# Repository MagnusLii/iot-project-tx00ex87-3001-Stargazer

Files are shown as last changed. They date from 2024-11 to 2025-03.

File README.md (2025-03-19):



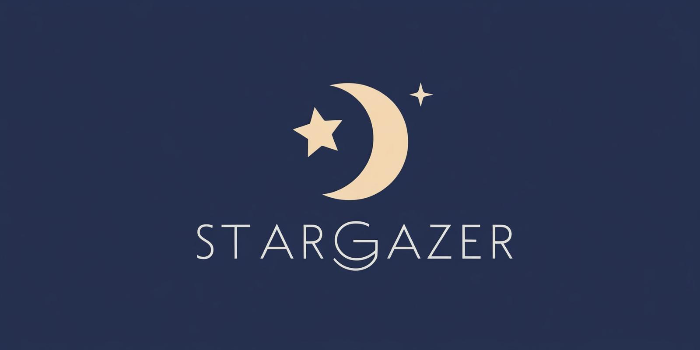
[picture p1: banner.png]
stargazer


  <p align="center">
    Amateur astronomy device

  </p>

<details>
  <summary>Table of Contents</summary>
  <ol>
    <li>
      <a href="#about-the-project">About The Project</a>
      <ul>
        <li><a href="#built-with">Built With</a></li>
      </ul>
    </li>
    <li>
      <a href="#getting-started">Getting Started</a>
      <ul>
        <li><a href="#prerequisites">Prerequisites</a></li>
        <li><a href="#installation">Installation</a></li>
      </ul>
    </li>
    <li><a href="#usage">Usage</a></li>
    <li><a href="#license">License</a></li>
  </ol>
</details>

## About The Project

The Stargazer is an easy to set up device that will take pictures of celestial objects at the most opportune times. Stargazer uses a simple and easy to use web interface to drive the device and see the beautiful pictures instantly when they happen. The pictures are also saved locally on an SD card for a convenient way of transferring and handling the pictures. Stargazer can also be driven completely offline using a laptop or a computer, making using the device flexible to use even when you have no internet connectivity.

### Built With

* [][Pico-SDK-url]
* [][ESP-idf-url]
* [][rustup-url]

## Getting Started

### Prerequisites

- ESP-idf: https://github.com/espressif/esp-idf
- Docker: https://www.docker.com/get-started/
- Rust: https://www.rust-lang.org/tools/install

See <a href="ASSEMBLY.md">ASSEMBLY.md</a> for details on building the physical device

**Optional:**
- Terminal connection software such as putty or minicom

### Installation

1. Clone the repo
   ```sh
   git clone https://gitlab.metropolia.fi/markulii/iot-project-tx00ex87-3001.git
   cd iot-project-tx00ex87-3001
   ```
2. Build Raspberry Pi Pico code with Docker
   ```sh
   cd pico
   docker compose up
   ```
3. Copy the binary to the Raspberry Pi Pico
    ```sh
    cp build/stargazer.uf2 <PATH TO PICO USB DEVICE PATH>
    ```

4. Build and flash ESP<br>
    Set the ESP into flash mode by connecting **GPIO0** to **GND** and power cycling the ESP.
    ```sh
    cd esp32-cam
    idf.py -p <PORT> flash
    ```
    Reboot the ESP out of flash mode by disconnecting **GPIO0** from **GND** and power cycling the ESP.
  
5. Build the webserver
   ```sh
   cd webserver
   ```
  - Option A. Build under repository directory
    ```sh
    cargo build --release
    ```
  - Option B. Build and install to Cargo install directory
    ```sh
    cargo install
    ```

## Usage

Run the server
  ```sh
    cargo run
  ```

* More details regarding the web server can be found <a href="webserver/README.md">here</a>

### Operating the device directly:
The device can be operated directly by connecting to the Pico via USB cable and opening a terminal connection with a baud rate of 115200.<br>
Sending any character puts the Pico into command mode which allows for using commands to operate the whole system.<br>

#### List of commands in configuration mode
`help` to see a list of all commands and their arguments.<br>
`exit` to exit command mode.<br>
`heading` to set compass heading of the device<br>
`time` to view or set current time<br>
`coord` to view or set current coordinates<br>
`instruction` to add an instruction directly to device<br>
`wifi` to set wifi details<br>
`server` to set the server details<br>
`token` to set the api token<br>

#### The following additional commands are available if debug build is compiled<br>

`debug_command` to add a command directly to the queue<br>
`debug_picture` to send a take picture message directly to the ESP<br>
`debug_rec_msg` to add a message (as if it came from the ESP) to the receive queue<br>
`debug_send_msg` to send a message to the ESP<br>
`debug_trace` to trace a planet with the device<br>

### Enabling operation from webserver:
When booting the device for the first time you'll need to provide the following for the Stargazer to connecto the webserver and run with full functionality.<br>
 - `Wifi SSID` - The ssid of your wireless network.
 - `Wifi password` - The password of your wireless network.
 - `Webserver domain` - The FQDN or IP address through which the server can be accessed.
 - `Webserver port` - The port used to communicated with the server (default is 8080).
 - `Webserver token` - Token generated in the webserver to enable API calls.

 **Optional:**

 - `Certificate` - Certificate to enable TLS connections. Only needed if you intend to use TLS to connect to your webserver.

 These settings can be set either by using the appropriate commands in direct control mode see: <a href="#direct-control">Operating the device directly:</a>

  alternatevly by setting them in a file called settings.txt on the SDcard connected to the ESP.<br>
  If creating the settings file the settings need to be in the same order as above with each setting on a new line.<br>
  The certificate needs to begin with `-----BEGIN CERTIFICATE-----` and end with `-----END CERTIFICATE-----`.

  **IMPORTANT:** The final line needs to include a 16bit crc in little endian ordering. A comma is prepended to the crc eg: `,4B37`<br>
  If any setting is missing or if the file is improperly formatted the device will not be able to initialize code/components related to said settings.<br>
  An example `settings.txt` can be found at <a href="example-settings.txt">/example-settings.txt.</a> <br>
  **NOTE:** the file must be renamed to `settings.txt`.<br>

  A third option is to define your values in `/esp32-cam/testMacros.hpp`, uncomment `# set(CMAKE_CXX_FLAGS "${CMAKE_CXX_FLAGS} -DSAVE_TEST_SETTINGS_TO_SDCARD")`<br>
  by removing the `#` in `/esp32-cam/CMakeLists.txt` and then build the project as described in <a href="#Build-and-flash-ESP">Build and flash ESP</a> <br>
  **NOTE:** Doing this will cause the settings defined in `/esp32-cam/testMacros.hpp` to be written onto `settings.txt` each time the ESP is restarted.

  <a href="#CMAKE-flags">Read here for more information about CMAKE flags</a> <br>

### Operating the device from the server:
The command options are as follows:<br>
* Target:<br>
`Sun`<br>`Moon`<br>`Mercury`<br>`Venus`<br>`Mars`<br>`Jupiter`<br>`Saturn`<br>`Uranus`<br>`Neptune`<br>
* Image Position:<br>
`Rising`: Takes a picture when the celestial object rises from the horizon.<br>
`Zenith`: Takes a picture at the zenith of the celestial object.<br>
`Setting`: Takes a picture when the celestial object close to setting beneath the horizon<br>
`Any`: Takes a picture at the current given time.<br>

## CMAKE flags
The following CMAKE flags can be enabled in <a href="esp32-cam/CMakeLists.txt">esp32-cam/CMakeLists.txt</a>.<br>
Enabling these flags changes the way the device operates.
 - set(CMAKE_CXX_FLAGS "${CMAKE_CXX_FLAGS} -DENABLE_ESP_DEBUG")<br>
   If enabled it will cause the ESP to send debug logs to the UART connection.<br>
   **NOTE:** These logs will cause problems for the pico and thus should not be turned on for normal operations, only if you wish to debug something.<br><br>
 - set(CMAKE_CXX_FLAGS "${CMAKE_CXX_FLAGS} -DUSE_TLS")<br>
   If enabled it will force the ESP to use TLS when connecting to the webserver.<br>
   **NOTE:** Due to the increased memory requirements of TLS this can cause the upload of larger images to fail due to insufficient memory on the AIthinker ESP32-cam module.<br><br>
 - set(CMAKE_CXX_FLAGS "${CMAKE_CXX_FLAGS} -DSAVE_TEST_SETTINGS_TO_SDCARD")<br>
   If enabled the ESP will write settings defined in `/esp32-cam/testMacros.hpp` to `settings.txt` on the SD card on boot.<br>
   This is useful if you do no wish to perform the other methods described in <a href="#Settings-file">Enabling operation from webserver</a>.<br>
   **NOTE:** Having this enabled will cause the settings to we written each time the ESP reboots causing settings to be lost if changed.

<!-- LICENSE -->
## License

Distributed under the ISC License. See `LICENSE` for more information.

<!-- MARKDOWN LINKS & IMAGES -->
<!-- https://www.markdownguide.org/basic-syntax/#reference-style-links -->
[contributors-shield]: https://img.shields.io/github/contributors/github_username/repo_name.svg?style=for-the-badge
[contributors-url]: https://github.com/github_username/repo_name/graphs/contributors

[repo-url]: https://gitlab.metropolia.fi/markulii/iot-project-tx00ex87-3001

[Pico-SDK-url]: https://github.com/raspberrypi/pico-sdk
[Pico-SDK-badge]: https://img.shields.io/badge/-RaspberryPi-C51A4A?style=for-the-badge&logo=Raspberry-Pi

[ESP-idf-url]: https://github.com/espressif/esp-idf
[ESP-IDF-badge]: https://img.shields.io/badge/Platform-ESP32-informational

[rustup-url]: https://www.rust-lang.org/tools/install
[rustup-badge]: https://img.shields.io/badge/Rust-%23000000.svg?e&logo=rust&logoColor=white&logoSize=20

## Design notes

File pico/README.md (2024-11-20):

# Building with Docker

1. Install Docker and Docker Compose
2. Run `docker compose up` in pico directory
3. After the build is complete, the binary will be available at `./build/pico-stargazer.{uf2|elf}` (Assuming it was successful)

# Flashing the Pico

## Using OpenOCD
- Make sure you have a Raspberry Pi Debug Probe or some other CMSIS-DAP device connected, and that you have OpenOCD installed (and in your PATH)
- Run the following command
```
$ openocd -f board/pico-debug.cfg -c "program build/pico-stargazer.elf verify reset exit"
```
- You may need to use `sudo` to run openocd depending on your system

## Copy the binary to the Pico
- Put the Pico into USB mass storage mode by holding down the BOOTSEL button and connecting it to your computer with a USB cable
- Copy the `pico-stargazer.uf2` file to the root of the USB drive

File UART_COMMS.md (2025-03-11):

## ESP & Pico communication
Protocol: UART<br>
Format: Custom Format<br>
example: `$<PREFIX>,<stuff>,<stuff2>,...<CRC>;`<br>
"$" Starts the message, ";" ends the message, `<PREFIX>` is the identifier for data, `<stuffX>` is data value.<br>

Celestial Object IDs:<br>
`<1>` = Sun<br>
`<2>` = Moon<br>
`<3>` = Mercury<br>
`<4>` = Venus<br>
`<5>` = Mars<br>
`<6>` = Jupiter<br>
`<7>` = Saturn<br>
`<8>` = Uranus<br>
`<9>` = Neptune<br>

Image position:<br>
`<1>` = Rising<br>
`<2>` = Zenith<br>
`<3>` = Setting<br>

Prefix values:<br>
`<0>` = unassigned/error<br>
`<1>` = ACK<br>
`<2>` = Datetime<br>
`<3>` = Device status check message<br>
`<4>` = ESP relaying command to Pico of what image to take.<br>
`<5>` = Command/Picture status from Pico to ESP<br>
`<6>` = Pico instructs ESP to take image<br>
`<7>` = Diagnostics data from Pico.         
`<8>` = WiFi information from Pico to ESP       
`<9>` = Send server ip/domain + (port) to ESP   
`<10>` = Api token from Pico to ESP             

Diagnostics values:<br>
`<1>` = Info<br>
`<2>` = Warning<br>
`<3>` = Error<br>

### Messages explained:

-   Datetime (Pico requests, ESP responds)<br>
    `$<2>,<1>,<CRC>;`<br>
    `$<2>,<Timestamp(int)>,<CRC>;` or `$<1>,<Bool>,<CRC>;` nack if not ready to send timestamp.<br>
    `$<1>,<Bool>,<CRC>;` True = ack, False nack.

-   Device init/status state message (ESP/Pico sends and other responds followed by final ack)<br>
    `$<3>,<Bool>,<CRC>;` True = ready, False = fire.<br>
    `$<3>,<Bool>,<CRC>;` True = ready, False = fire.<br>
    `$<1>,<Bool>,<CRC>;` True = ack, False nack.

-   Image taking process<br>
    ESP sends id of object to take picture of.<br>
    Pico sends (n)ack.<br>

    `$<4>,<Celestial object ID (int)>,<Image/command ID (int)>,<Position>,<CRC>;`<br>
    `$<1>,<Bool>,<CRC>;` True = ack, False nack.<br>

    Pico sends Command status message to ESP which it relays to the server.<br>
    ESP sends (n)ack.<br>

    `$<5>,<Image/command ID (int)>,<Status (int),<Time (int)>,<CRC>;`<br>
    `$<1>,<Bool>,<CRC>;` True = ack, False nack.<br>

    _Some time usually passes._<br>

    Pico sends take image message when the device is pointed at the celestial object and it's time to take a picture.<br>
    ESP takes picture and sends confirmation to Pico.<br>

    `$<6>,<Image/command ID (int)>,<CRC>;`<br>
    `$<1>,<Bool>,<CRC>;` True = ack, False nack.<br>

-   Diagnostics data from Pico.<br>
    `$<7>,<Status (int)>,<Message (string)>,<CRC>;`<br>
    `$<1>,<Bool>,<CRC>;` True = ack, False nack.<br>

-   Configuration messages from Pico.<br>

    Wi-Fi details<br>
    `$<8>,<SSID (string)>,<Password (string)>,<CRC>;`<br>
    `$<1>,<Bool>,<CRC>;` True = ack, False nack.<br>

    Server details<br>
    `$<9>,<IP/domain (string)>,<Port (int)>,<CRC>;` #if port = 0, port is unused<br>
    `$<1>,<Bool>,<CRC>;` True = ack, False nack.<br>

    API token<br>
    `$<10>,<Token (string)>,<CRC>;`<br>
    `$<1>,<Bool>,<CRC>;` True = ack, False nack.<br>

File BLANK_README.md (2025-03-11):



<h1 align="center">Stargazer</h1>

  <p align="center">
    Amateur astronomy device

  </p>

<details>
  <summary>Table of Contents</summary>
  <ol>
    <li>
      <a href="#about-the-project">About The Project</a>
      <ul>
        <li><a href="#built-with">Built With</a></li>
      </ul>
    </li>
    <li>
      <a href="#getting-started">Getting Started</a>
      <ul>
        <li><a href="#prerequisites">Prerequisites</a></li>
        <li><a href="#installation">Installation</a></li>
      </ul>
    </li>
    <li><a href="#usage">Usage</a></li>
    <li><a href="#license">License</a></li>
  </ol>
</details>

<!-- ABOUT THE PROJECT -->
## About The Project

The Stargazer is an easy to set up device that will take pictures of celestial objects at the most opportune times. Stargazer uses a simple and easy to use web interface to drive the device and see the beautiful pictures instantly when they happen. The pictures are also saved locally on an SD card for a convenient way of transferring and handling the pictures. Stargazer can also be driven completely offline using a laptop or a computer, making using the device flexible to use even when you have no internet connectivity.

<p align="right">(<a href="#readme-top">back to top</a>)</p>

### Built With

* [][Pico-SDK-url]
* [][ESP-idf-url]
* [][rustup-url]

<p align="right">(<a href="#readme-top">back to top</a>)</p>

## Getting Started

This is an example of how you may give instructions on setting up your project locally.
To get a local copy up and running follow these simple example steps.

### Prerequisites

This is an example of how to list things you need to use the software and how to install them.
- ESP-idf: https://github.com/espressif/esp-idf
- Docker: https://www.docker.com/get-started/
- Rust: https://www.rust-lang.org/tools/install

See <LINK TO ASSEMBLY MD> for details on building the physical device

optional:
- Terminal connection software such as putty or minicom

### Installation

1. Clone the repo
   ```sh
   git clone https://gitlab.metropolia.fi/markulii/iot-project-tx00ex87-3001.git
   cd iot-project-tx00ex87-3001
   ```
2. Build Raspberry Pi Pico code with Docker
   ```sh
   cd pico
   docker compose up
   ```
3. Copy the binary to the Raspberry Pi Pico
    ```sh
    cp build/stargazer.uf2 <PATH TO PICO USB DEVICE PATH>
    ```
4. Build and flash ESP<br>
    Set the ESP into flash mode.
    ```sh
    cd esp32-cam
    idf.py -p <PORT> flash
    ```
    Reboot the ESP out of flash mode.
  
5. Build the webserver
   ```sh
   cd webserver
   ```
  - Option A. Build under repository directory
    ```sh
    cargo build --release
    ```
  - Option B. Build and install to Cargo install directory
    ```sh
    cargo install
    ```

<p align="right">(<a href="#readme-top">back to top</a>)</p>

## Usage

Run the server
  ```sh
    cargo run
  ```

### - Operating the device directly:
The device can be operated directly by connecting to the Pico via USB cable and opening a terminal connection with a baud rate of 115200.<br>
Sending any character puts the Pico into command mode which allows for using commands to operate the whole system.<br>

#### List of commands in configuration mode
`help` to see a list of all commands and their arguments.<br>
`exit` to exit command mode.<br>
`heading` to set compass heading of the device<br>
`time` to view or set current time<br>
`coord` to view or set current coordinates<br>
`instruction` to add an instruction directly to device<br>
`wifi` to set wifi details<br>
`server` to set the server details<br>
`token` to set the api token<br>

#### The following additional commands are available if debug build is compiled<br>

`debug_command` to add a command directly to the queue<br>
`debug_picture` to send a take picture message directly to the ESP<br>
`debug_rec_msg` to add a message (as if it came from the ESP) to the receive queue<br>
`debug_send_msg` to send a message to the ESP<br>
`debug_trace` to trace a planet with the device<br>

### Enabling operation from webserver:
When booting the device for the first time you'll need to provide the following for the Stargazer to connecto the webserver and run with full functionality.<br>
 - `Wifi SSID` - The ssid of your wireless network.
 - `Wifi password` - The password of your wireless network.
 - `Webserver domain` - The FQDN or IP address through which the server can be accessed.
 - `Webserver port` - The port used to communicated with the server (default is 8080).
 - `Webserver token` - Token generated in the webserver to enable API calls.
 Optional:
 - `Certificate` - Certificate to enable TLS connections. Only needed if you intend to use TLS to connect to your webserver.

 These settings can be set either by using the appropriate commands in direct control mode see: 
 
 <p align="left"><a href="#direct-control">### - Operating the device directly:</a></p>

  or by setting them in a file called settings.txt on the SDcard connected to the ESP.<br>
  If creating the settings file the settings need to be in the same order as above with each setting on a new line.<br>
  The certificate needs to begin with `-----BEGIN CERTIFICATE-----` and end with `-----END CERTIFICATE-----`.

  IMPORTANT: The final line needs to include a 16bit crc in little endian ordering. A comma is prepended to the crc eg: `,4B37`<br>
  If any setting is missing or if the file is improperly formatted the device will not be able to initialize code/components related to   said settings.

### Operating the device from the server:
The command options are as follows:<br>
* Target:<br>
`Sun`<br>`Moon`<br>`Mercury`<br>`Venus`<br>`Mars`<br>`Jupiter`<br>`Saturn`<br>`Uranus`<br>`Neptune`<br>
* Image Position:<br>
`Rising`: Takes a picture when the celestial object rises from the horizon.<br>
`Zenith`: Takes a picture at the zenith of the celestial object.<br>
`Any`: Takes a picture at the current given time.<br>

<p align="right">(<a href="#readme-top">back to top</a>)</p>

<!-- LICENSE -->
## License

Distributed under the ISC License. See `LICENSE` for more information.

<p align="right">(<a href="#readme-top">back to top</a>)</p>

<!-- MARKDOWN LINKS & IMAGES -->
<!-- https://www.markdownguide.org/basic-syntax/#reference-style-links -->
[contributors-shield]: https://img.shields.io/github/contributors/github_username/repo_name.svg?style=for-the-badge
[contributors-url]: https://github.com/github_username/repo_name/graphs/contributors

[repo-url]: https://gitlab.metropolia.fi/markulii/iot-project-tx00ex87-3001

[Pico-SDK-url]: https://github.com/raspberrypi/pico-sdk
[Pico-SDK-badge]: https://img.shields.io/badge/-RaspberryPi-C51A4A?style=for-the-badge&logo=Raspberry-Pi

[ESP-idf-url]: https://github.com/espressif/esp-idf
[ESP-IDF-badge]: https://img.shields.io/badge/Platform-ESP32-informational

[rustup-url]: https://www.rust-lang.org/tools/install
[rustup-badge]: https://img.shields.io/badge/Rust-%23000000.svg?e&logo=rust&logoColor=white&logoSize=20

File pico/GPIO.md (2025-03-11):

#  PINS
### 1 - GP0       - UART0 TX - ESP RX
### 2 - GP1       - UART0 RX - ESP TX
### 3 - GND       - 
### 4 - GP2       - 
### 5 - GP3       - 
### 6 - GP4       - UART1 TX - GPS RX
### 7 - GP5       - UART1 RX - GPS TX
### 8 - GND       - 
### 9 - GP6       - LN4 - MOTOR HORIZONTAL
### 10 - GP7      - LN3 - MOTOR HORIZONTAL
### 11 - GP8      - LN2 - MOTOR HORIZONTAL
### 12 - GP9      - LN1 - MOTOR HORIZONTAL
### 13 - GND      - 
### 14 - GP10     - OPTO HORIZONTAL
### 15 - GP11     - 
### 16 - GP12     - 
### 17 - GP13     - 
### 18 - GND      - 
### 19 - GP14     - 
### 20 - GP15     - OPTO VERTICAL
### 21 - GP16     - I2C0 SDA - COMPASS
### 22 - GP17     - I2C0 SCL - COMPASS
### 23 - GND      - 
### 24 - GP18     - LN4 - MOTOR VERTICAL
### 25 - GP19     - LN3 - MOTOR VERTICAL
### 26 - GP20     - LN2 - MOTOR VERTICAL
### 27 - GP21     - LN1 - MOTOR VERTICAL
### 28 - GND      - 
### 29 - GP22     - 
### 30 - RUN      - 
### 31 - GP26     - I2C1 SDA - EEPROM
### 32 - GP27     - I2C1 SCL - EEPROM
### 33 - GND      - 
### 34 - GP28     - 
### 35 - ADC_VREF -  
### 36 - 3V3OUT   - 
### 37 - 3V3EN    - 
### 38 - GND      - GND - ESP (any ground pin will do)
### 39 - VSYS     - 5V - ESP
### 40 - VBUS     -

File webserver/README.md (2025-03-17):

# Requirements
- Cargo/rustc (build, tested on version 1.84)

# Building

## Option A. Build only
```sh
cargo build --release
```
## Option B. Build and install to Cargo binary directory
```sh
cargo install
```

# Configuration
Server configuration can be set in a `config.toml` file which the program will look for in the current working directory by default.<br>

You can also specify a config file as an argument to the program.<br>

All available configuration options can be found in the <a href="example-config.toml">example-config.toml</a>

# Usage
```
Stargazer webserver

Usage: stargazer-ws [OPTIONS]

Options:
  -a, --address <ADDRESS>          Set server address
  -p, --port-http <PORT_HTTP>      Set HTTP port
  -s, --port-https <PORT_HTTPS>    Set HTTPS port
      --disable-http               Disable HTTP
      --enable-http                Enable HTTP
      --enable-http-api            Enable HTTP API if HTTP is disabled
      --disable-https              Disable HTTPS
      --enable-https               Enable HTTPS
      --enable-https-api           Enable HTTPS API if HTTPS is disabled
  -c, --config-file <CONFIG_FILE>  Set config file to use (default: config.toml)
  -w, --working-dir <WORKING_DIR>  Set working directory
      --db-dir <DB_DIR>            Set database directory
      --assets-dir <ASSETS_DIR>    Set assets directory
      --certs-dir <CERTS_DIR>      Set certificate directory
  -h, --help                       Print help
  -V, --version                    Print version
```

## Option A
#### You can run the server using
```sh
cargo run --
```
#### or by running the executable directly (located under target/<build_type>/)
```sh
cd target/release/
./stargazer-ws
```

## Option B
#### You can run the server from anywhere (provided that the Cargo bin dir is in your path)
```sh
stargazer-ws
```

## Web interface
When starting up the server for the first time you can login using the default credentials:<br>
Username: admin<br>
Password: admin<br>

* You can change the username and/or password of the admin account on the user page, which you can get to by clicking the account name in the navigation bar/menu.<br>

### Quick start instructions

You need to first create a key from the `Keys` page which can be accessed from the `Control` page before you can add commands to the queue.<br>
Generating a key is as simple as giving it a name then pressing generate.<br>
Then you can copy and give the key/token to the Stargazer device<br><br>

After that is done you can add commands from the `Control`/`Commands` page.<br>

The command options are as follows:<br>
* Target:<br>
`Sun`<br>`Moon`<br>`Mercury`<br>`Venus`<br>`Mars`<br>`Jupiter`<br>`Saturn`<br>`Uranus`<br>`Neptune`<br>
* Image Position:<br>
`Rising`: Takes a picture when the celestial object rises from the horizon.<br>
`Zenith`: Takes a picture at the zenith of the celestial object.<br>
`Setting`: Takes a picture when the celestial object close to setting beneath the horizon
`Any`: Takes a picture at the current given time.<br>

# API
The API currently has the following endpoints:

- `/api/upload` (POST)
- `/api/command` (GET, POST)
- `/api/diagnostics` (POST)
- `/api/time` (GET)

More details can be found in API.md

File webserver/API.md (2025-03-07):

# API
The API currently has the following endpoints:

- `/api/upload` (POST)
- `/api/command` (GET, POST)
- `/api/diagnostics` (POST)
- `/api/time` (GET)

## `/api/upload`
Uploads an image wrapped in JSON to the webserver.

The JSON should contain the following fields:

- `token`: The API token (string)
- `id`: The ID of the command (int)
- `data`: The base64 encoded image (string)

Example:
```
curl -H "Content-Type: application/json" --request POST --data @img.json 127.0.0.1:7878/api/upload
```
where @img.json contains:
```
{
    "token":"<api_token>",
    "id":<id>,
    "data":"<base64_data>"
}
```

## `/api/command`
### GET
Fetch a command from the webserver.

Example:
```
curl "127.0.0.1:7878/api/command?token=<api_token>"
```

Returns a JSON object with the following fields:
- `target`: The target object (int)
- `id`: The ID of the command/picture (int)
- `position`: The position to take the photo (int) {1,2,3}

Or an empty object if no command is available

### POST
Send a response in JSON to the webserver.

The JSON should contain the following fields:

- `token`: The API token (string)
- `id`: The ID of the command (int)
- `status`: The command status (int)
```
Command status: (-)1 = Fetch, (-)2 = Calculate, ((-)3 = Picture)
Negative sign indicates error in said stage.
```

Optional fields:
- `time`: The estimated time to take the photo (int) [NOTE: unix epoch time sent along with status 2]

Example:
```
curl -H "Content-Type: application/json" --request POST --data "{\"token\":\"ae07ddd0-5dc1-47d2-98ab-9cea274f1f61\",\"id\":1,\"status\":2}" 127.0.0.1:7878/api/command
```

## `/api/diagnostics`
Send diagnostics to the webserver.

The JSON should contain the following fields:

- `token`: The API token (string)
- `status`: The status (int)
- `message`: The message (string)

## `/api/time`
Get the current time from the webserver.

Example:
```
curl "127.0.0.1:7878/api/time"
```

Returns time in seconds since epoch

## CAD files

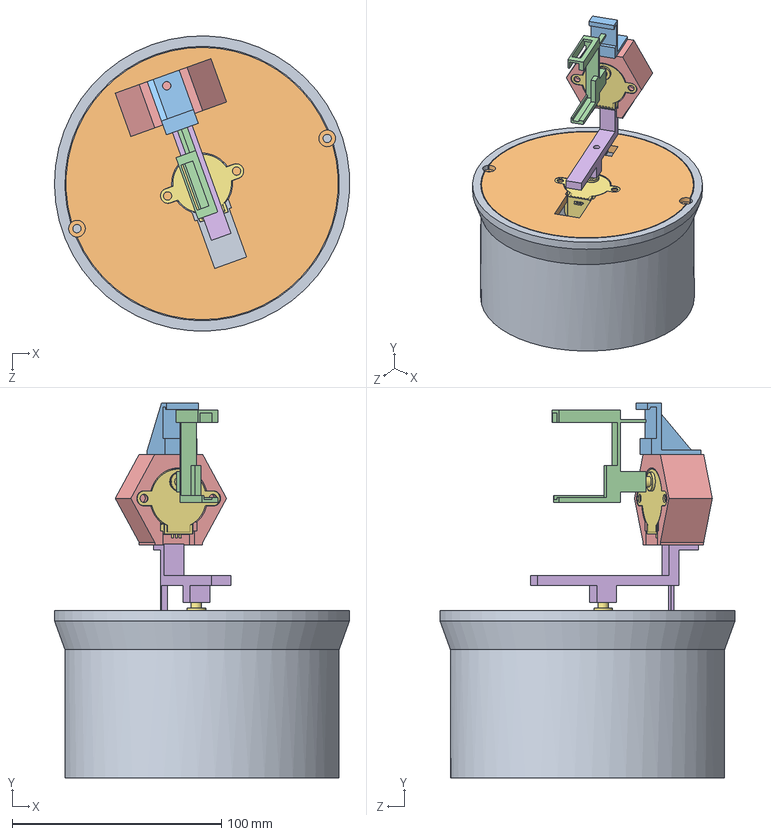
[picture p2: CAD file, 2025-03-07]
3D-models/Gyro-arm-assembly.SLDASM
140.9 x 179.0 x 140.9 mm
28BYJ-48-stepper-motor x 2
Connector-arm
28BYJ-48-cover
ESP-Holder
Opto-fork-holder
28BYJ-48-bottom-plate
Bottom-bowl

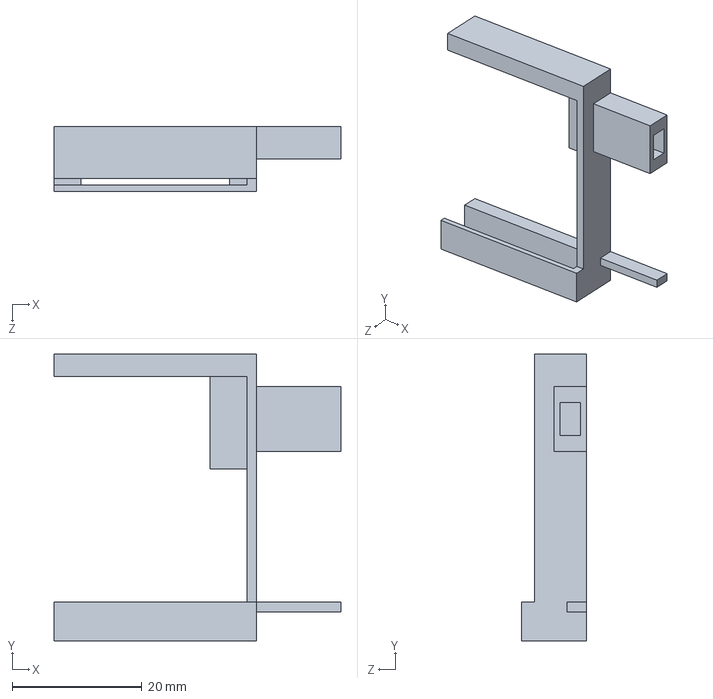
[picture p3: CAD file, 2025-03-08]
3D-models/ESP-Holder.SLDPRT
44.2 x 44.2 x 10.0 mm

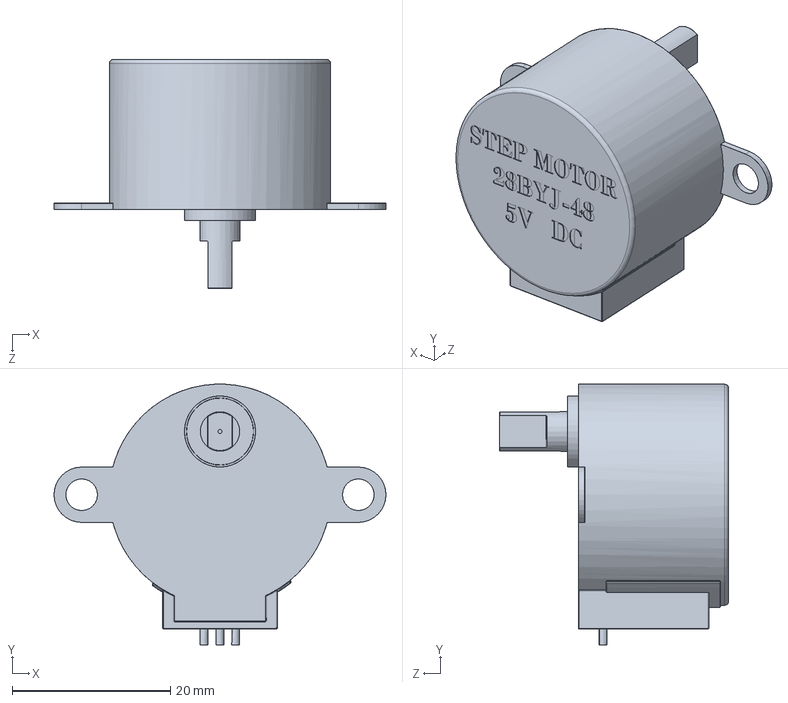
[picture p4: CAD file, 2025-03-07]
3D-models/28BYJ-48-stepper-motor.sldprt
42.0 x 33.0 x 29.0 mm

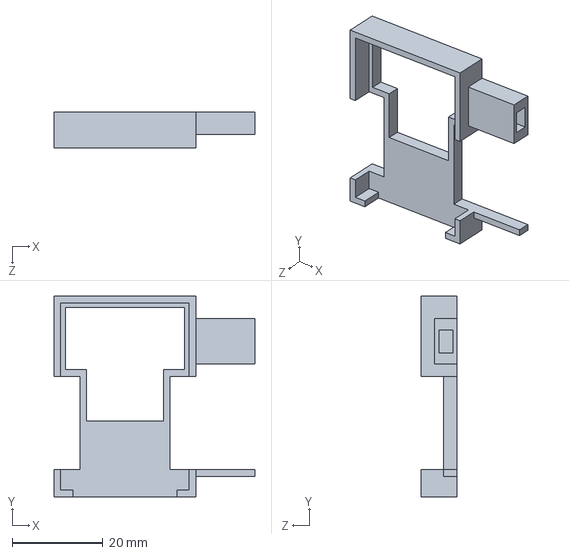
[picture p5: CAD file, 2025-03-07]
3D-models/ESP-Holder - BACKUP.SLDPRT
44.2 x 44.2 x 8.00 mm

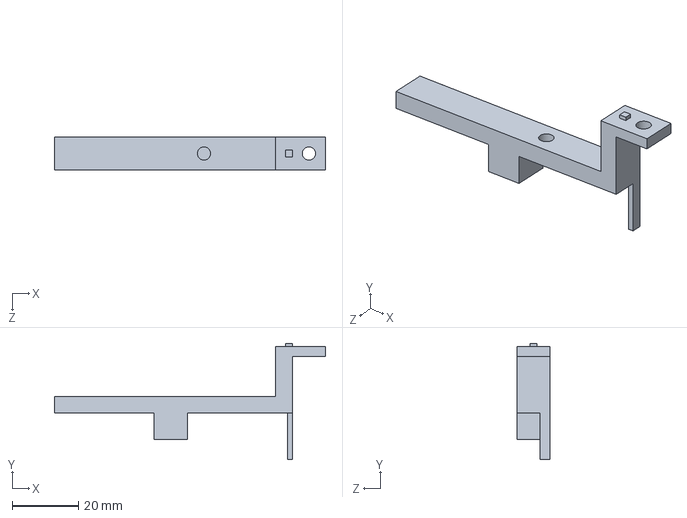
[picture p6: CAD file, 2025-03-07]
3D-models/Connector-arm.SLDPRT
81.6 x 35.0 x 10.0 mm

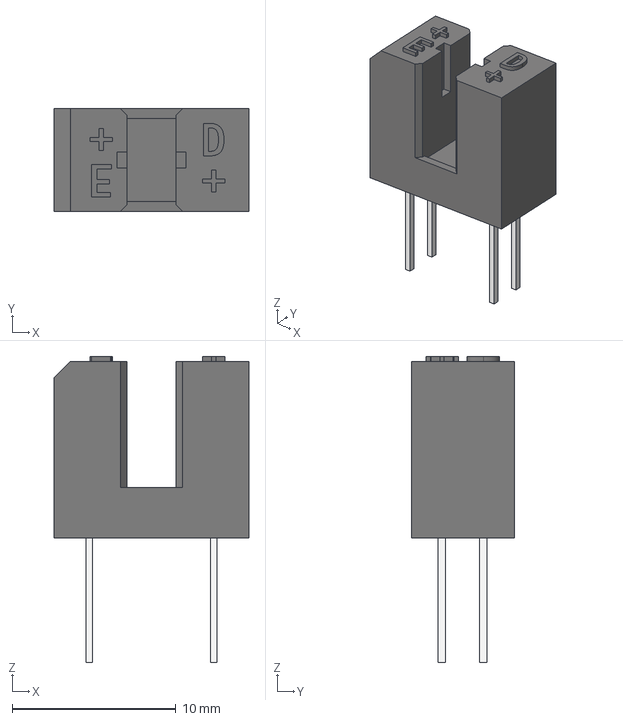
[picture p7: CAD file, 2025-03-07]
3D-models/TCST1103.stp
11.9 x 6.30 x 18.7 mm

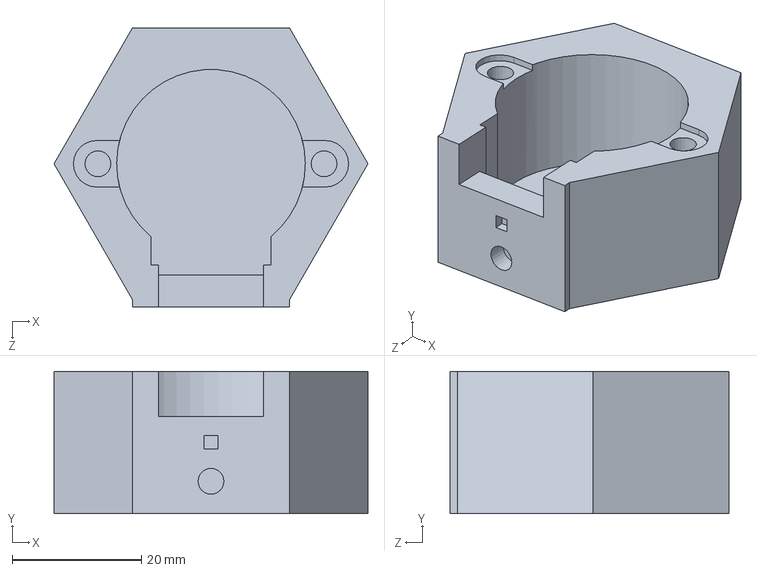
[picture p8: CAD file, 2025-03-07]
3D-models/28BYJ-48-cover.SLDPRT
48.6 x 22.0 x 43.2 mm

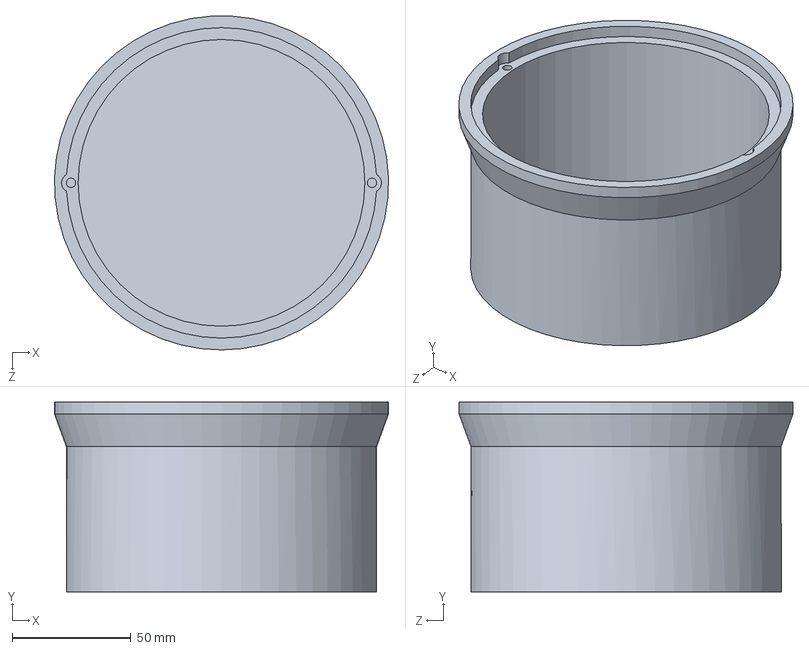
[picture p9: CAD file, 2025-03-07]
3D-models/Bottom-bowl.SLDPRT
140.9 x 80.0 x 140.9 mm

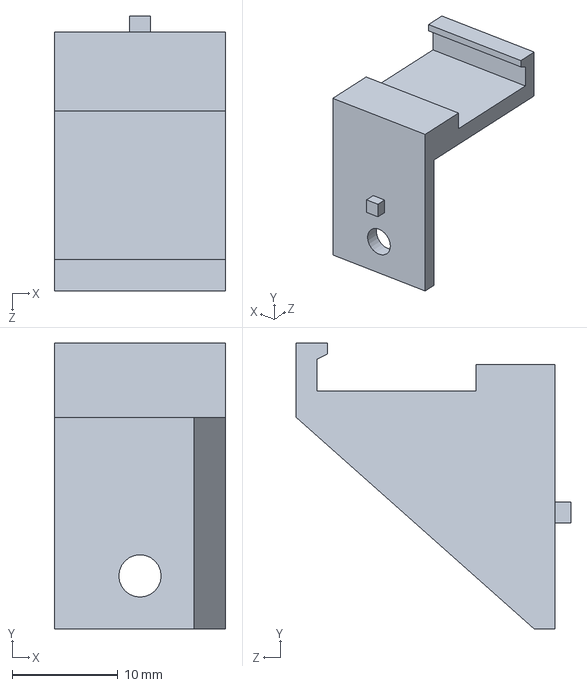
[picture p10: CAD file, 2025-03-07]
3D-models/Opto-fork-holder.SLDPRT
16.2 x 27.0 x 26.0 mm

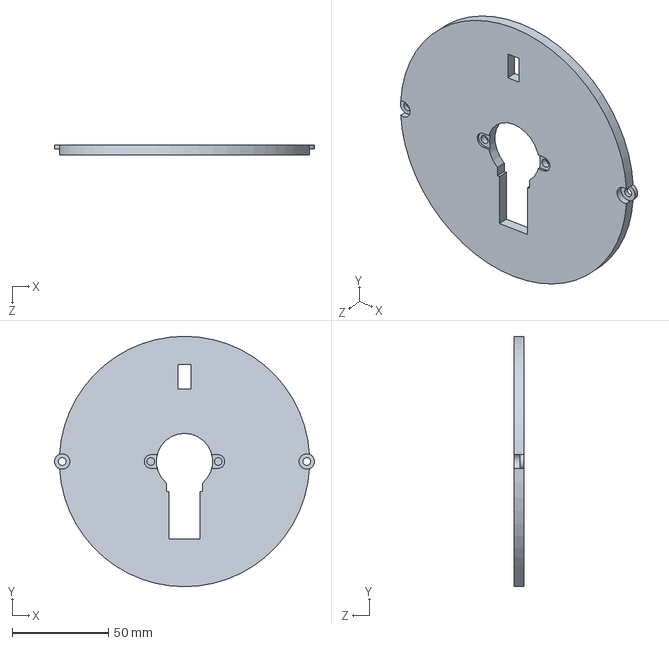
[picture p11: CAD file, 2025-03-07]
3D-models/28BYJ-48-bottom-plate.SLDPRT
135.0 x 130.0 x 5.00 mm

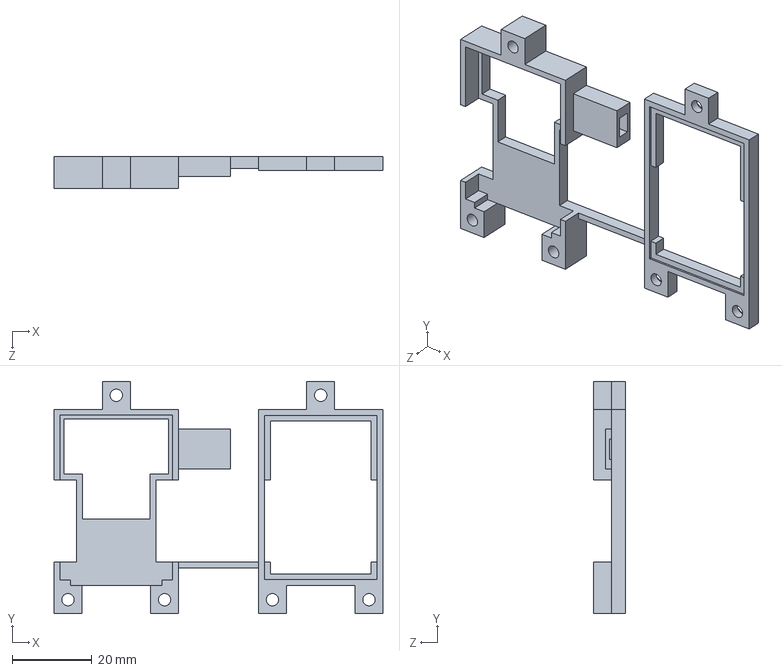
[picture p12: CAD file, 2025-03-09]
3D-models/ESP-Holder-Nut-Lock-Design.SLDPRT
82.4 x 58.2 x 8.00 mm

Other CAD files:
3D-models/STL/28BYJ-48-bottom-plate.STL
3D-models/STL/28BYJ-48-cover.STL
3D-models/STL/Bottom-bowl.STL
3D-models/STL/Connector-arm.STL
3D-models/STL/ESP-Holder-Nut-Lock-Design.STL
3D-models/STL/ESP-Holder.STL
3D-models/STL/Opto-fork-holder.STL

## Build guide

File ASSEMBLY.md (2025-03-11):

# Instructions for assembling the Stargazer

## Requirements
- 3D printer
- 8 M3-0.5 heat inserts
- 8 M3 screws
- Electrical tape
- Pico or PicoW (H or WH versions also work)
- AIthinker esp-cam32
- Jumper wires
- 2 grove cables
- 2 28BYJ-48 stepper motors
- 2 6pin Stepper motor drivers
- Crowtail three-axis compass
- Mikroe GPS3 click gps
- Crowtail I2C EEPROM
- 2 TCST1103 opto forks

optional:
- Soldering board(s)

if using nut-lock version of ESP-Holder:<br>
- 3 M3 screws
- 3 M3 nuts

## 3D prints
STL files for printing can be found under `/3D-models/STL`.<br>
Files for 3D models can be found under `/3D-models`.<br>

3D-Models/Gyro-arm-assembly.SLDASM can be used to view the entire assembly as intended to be assembled in solidworks.<br>

Note: There are two files for ESP-holder, both designs work however one locks the ESP more securely. Only one is needed for the Stargazer.

## Assembly

### 3D printed parts and components
Some of the parts are designed to have M3-0.5 heat inserts inserted into them to enable using screws to securely connect the parts.<br>
- The <a href="3D-models/STL/Bottom-bowl.STL">Bottom-bowl</a> is mean to contain most of the electronics and and acts as the stand for the Stargazer.<br>
- The <a href="3D-models/STL/28BYJ-48-bottom-plate.STL">28BYJ-48-Bottom-plate</a> acts as a cover for the bowl and a platform for the camera gyro setup.<br>
Two screw placements are provided to securely mount the plate to the bowl. The plate has a hole for the horizontal bottom motor and opto fork sensor.<br>
There are two insert holes next to the central motor hole to screw the motor onto the plate.<br>
- The <a href="3D-models/STL/Connector-arm.STL">Connector-arm</a> connects the bottom horizontal motor to the <a href="3D-models/STL/28BYJ-48-cover.STL">28BYJ-48-cover</a> which houses the top vertical motor. This connection requres one screw/insert.
- The <a href="3D-models/STL/Opto-fork-holder.STL">Opto-fork-holder</a> is placed ontop of the <a href="3D-models/STL/Connector-arm.STL">Connector-arm</a> and is meant to hold the vertical TCST1103 opto fork. Note our opto forks has custom printed circuit boards which we do not have the files for there fore this <a href="3D-models/STL/Opto-fork-holder.STL">Opto-fork-holder</a> design will not work with most cases.
- And finally the <a href="3D-models/STL/ESP-Holder-Nut-Lock-Design.STL">ESP-Holder</a> connects to the vertical motor without screws and holds the ESP.
- All the other components are located in the bottom bowl.

### Microcontroller wiring
Wiring pins can be seen in <a href="pico/GPIO.md">pico/GPIO.MD</a>, all other devices/motors/sensors are wired directly to the Pico.

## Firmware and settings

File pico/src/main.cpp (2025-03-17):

#include "pico/stdlib.h" // IWYU pragma: keep

#include "PicoUart.hpp"
#include "clock.hpp"
#include "commbridge.hpp"
#include "compass.hpp"
#include "controller.hpp"
#include "debug.hpp"
#include "gps.hpp"
#include "message.hpp"
#include "motor-control.hpp"
#include "stepper-motor.hpp"
#include "storage.hpp"

#include <memory>
#include <queue>

int main() {
    stdio_init_all();
    sleep_ms(500);
    DEBUG("Boot");

    auto uart_0 = std::make_shared<PicoUart>(0, 0, 1, 115200);
    DEBUG("UART0 initialized");
    auto uart_1 = std::make_shared<PicoUart>(1, 4, 5, 9600);
    DEBUG("UART1 initialized");
    sleep_ms(50);

    auto clock = std::make_shared<Clock>();
    DEBUG("Clock initialized");
    auto gps = std::make_shared<GPS>(uart_1, false, true);
    DEBUG("GPS initialized");
    auto compass = std::make_shared<Compass>(i2c0, 17, 16);
    DEBUG("Compass initialized");
    auto storage = std::make_shared<Storage>(i2c1, 26, 27);

    auto queue = std::make_shared<std::queue<msg::Message>>();
    DEBUG("Queue initialized");
    auto commbridge = std::make_shared<CommBridge>(uart_0, queue);
    DEBUG("CommBridge initialized");

    const std::vector<uint> pins1{6, 7, 8, 9};
    DEBUG("Stepper motor pins initialized");
    const std::vector<uint> pins2{18, 19, 20, 21};
    DEBUG("Stepper motor pins initialized");
    const int opto_horizontal = 10;
    const int opto_vertical = 15;

    auto mh = std::make_shared<StepperMotor>(pins1);
    DEBUG("Stepper motor initialized");
    auto mv = std::make_shared<StepperMotor>(pins2);
    DEBUG("Stepper motor initialized");
    auto mctrl = std::make_shared<MotorControl>(mh, mv, opto_horizontal, opto_vertical);
    DEBUG("MotorControl initialized");

    Controller controller(clock, gps, compass, commbridge, mctrl, storage, queue);
    DEBUG("Controller initialized");
    for (;;) {
        controller.run();

        DEBUG("Returned from main loop");
        sleep_ms(1000);
    }
}

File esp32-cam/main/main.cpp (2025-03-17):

#include <esp_event.h>
#include <esp_log.h>
#include <esp_system.h>
#include <nvs_flash.h>
#include <stdio.h>
#include <stdlib.h>
#include <sys/param.h>

#include "freertos/FreeRTOS.h"
#include "freertos/task.h"

#include "driver/sdmmc_defs.h"
#include "driver/sdmmc_host.h"
#include "esp_vfs_fat.h"
#include "sdmmc_cmd.h"

#include "TaskPriorities.hpp"
#include "camera.hpp"
#include "debug.hpp"
#include "requestHandler.hpp"
#include "sd-card.hpp"
#include "testMacros.hpp"
#include "wireless.hpp"
#include <memory>

#include "esp_sntp.h"
#include "tasks.hpp"
#include "timesync-lib.hpp"

#include "espPicoUartCommHandler.hpp"
#include "message.hpp"

#include "esp_task_wdt.h"

#include "mbedtls/platform.h"

#include <set>

extern "C" {
void app_main(void);
}
void app_main(void) {
    DEBUG("Starting main");
    vTaskDelay(pdMS_TO_TICKS(1000));

    xTaskCreate(init_task, "init-task", 8192, NULL, TaskPriorities::HIGH, NULL);

    while (1) {
        vTaskDelay(pdMS_TO_TICKS(10000));
    }
}

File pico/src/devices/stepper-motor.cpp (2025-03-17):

#include "stepper-motor.hpp"
#include "stepper.pio.h"
#include "structs.hpp"

int modulo(int x, int y) {
    int rem = x % y;
    return rem + ((rem < 0) ? y : 0);
}

StepperMotor::StepperMotor(const std::vector<uint> &stepper_pins)
    : pins(stepper_pins), direction(true), pioInstance(nullptr), programOffset(0), stateMachine(0), speed(0),
      sequenceCounter(0), stepCounter(0), stepMax(4097), stepMemory(0) {
    // need 4 pins
    if (pins.size() != 4) panic("Need 4 pins to operate stepper motor. number of pins got: %d", pins.size());
    // Three first stepper pins must be less than 6 apart
    if (pins[2] - pins[0] > 5)
        panic("Three first stepper pins must be less than 6 apart. They are %d apart", pins[2] - pins[0]);
}

void StepperMotor::init(PIO pio, float rpm, bool clockwise) {
    pioInstance = pio;
    speed = rpm;
    direction = clockwise;
    pioInit();
    pins_init();
    pio_sm_set_enabled(pioInstance, stateMachine, true);
}

// this doesn't set the statemachine running
void StepperMotor::pioInit(void) {
    if (direction) {
        programOffset = pio_add_program(pioInstance, &stepper_clockwise_program);
    } else {
        programOffset = pio_add_program(pioInstance, &stepper_anticlockwise_program);
    }
    pio_sm_config conf = stepper_clockwise_program_get_default_config(programOffset);
    sm_config_set_clkdiv(&conf, calculateClkDiv(speed));
    stateMachine = pio_claim_unused_sm(pioInstance, true);
    pio_sm_init(pioInstance, stateMachine, programOffset, &conf);
}

float StepperMotor::calculateClkDiv(float rpm) const {
    if (rpm > RPM_MAX) rpm = RPM_MAX;
    if (rpm < RPM_MIN) rpm = RPM_MIN;
    return (SYS_CLK_KHZ * 1000) / (16000 / (((1 / rpm) * 60 * 1000) / 4096));
}

// needs to be called after initializing PIO and statemachine
// The pins have to be ascending in order
void StepperMotor::pins_init() {
    // mask is needed to set pin directions in the state machine
    uint32_t pin_mask = 0x0;
    for (uint pin : pins) {
        pin_mask |= 1 << pin;
        pio_gpio_init(pioInstance, pin);
    }
    pio_sm_set_pindirs_with_mask(pioInstance, stateMachine, pin_mask, pin_mask);
    // Configure the set pins (first 3 pins) and the sideset pin (last pin)
    pio_sm_set_set_pins(pioInstance, stateMachine, pins[0], pins[2] - pins[0] + 1);
    pio_sm_set_sideset_pins(pioInstance, stateMachine, pins[3]);
    // this changes the statemachines bytecode to match the pins used.
    morph_pio_pin_definitions();
}

// this needs to be ran everytime the program changes!! (changing directions etc)
// changes the statemachines bytecode to match the pin layout
void StepperMotor::morph_pio_pin_definitions(void) {
    // TODO: make a cool equation to reduce code duplication
    uint pin1 = 1;
    uint pin2 = 1 << (pins[1] - pins[0]);
    uint pin3 = 1 << (pins[2] - pins[0]);
    std::vector<uint> instructions;
    instructions.reserve(8);
    // pin1
    instructions.emplace_back(pio_encode_set(pio_pins, pin1) | pio_encode_delay(7) | pio_encode_sideset(2, 0b10));
    // pin1 and 2
    instructions.emplace_back(pio_encode_set(pio_pins, pin1 | pin2) | pio_encode_delay(7) |
                              pio_encode_sideset(2, 0b10));
    // pin2
    instructions.emplace_back(pio_encode_set(pio_pins, pin2) | pio_encode_delay(7) | pio_encode_sideset(2, 0b10));
    // pin2 and pin 3
    instructions.emplace_back(pio_encode_set(pio_pins, pin2 | pin3) | pio_encode_delay(7) |
                              pio_encode_sideset(2, 0b10));
    // pin3
    instructions.emplace_back(pio_encode_set(pio_pins, pin3) | pio_encode_delay(7) | pio_encode_sideset(2, 0b10));
    // pin3 and pin4 (sideset)
    instructions.emplace_back(pio_encode_set(pio_pins, pin3) | pio_encode_delay(7) | pio_encode_sideset(2, 0b11));
    // no first 3 pins active pin4 active (sideset)
    instructions.emplace_back(pio_encode_set(pio_pins, 0) | pio_encode_delay(7) | pio_encode_sideset(2, 0b11));
    // pin1 and pin4 (sideset)
    instructions.emplace_back(pio_encode_set(pio_pins, pin1) | pio_encode_delay(7) | pio_encode_sideset(2, 0b11));
    if (!direction) { std::reverse(instructions.begin(), instructions.end()); }
    for (int i = 0; i < 8; i++) {
        pioInstance->instr_mem[programOffset + stepper_clockwise_offset_loop + i * 3] = instructions[i];
    }
}

void StepperMotor::turnSteps(uint16_t steps) {
    uint32_t word = ((programOffset + stepper_clockwise_offset_loop + 3 * sequenceCounter) << 16) | (steps);
    pio_sm_put_blocking(pioInstance, stateMachine, word);

    sequenceCounter = modulo(sequenceCounter + steps, 8);
    int16_t stepsToAdd = direction ? steps : -steps;
    stepCounter = modulo(stepCounter + stepsToAdd, stepMax);
    stepMemory = (stepMemory << 16) | stepsToAdd;
}

// this will stop the motor and turn to an angle instantly
void StepperMotor::turn_to(double radians) {
    stop();
    double current = get_position();
    double normalized = normalize_radians(radians);
    double distance = normalized - current;
    if (distance < -M_PI) { distance += 2 * M_PI; }
    if (distance > M_PI) { distance -= 2 * M_PI; }
    if (distance < 0)
        setDirection(ANTICLOCKWISE);
    else
        setDirection(CLOCKWISE);
    turnSteps(radians_to_steps(fabs(distance)));
}

void StepperMotor::turnOneRevolution() { turnSteps(stepMax); }

void StepperMotor::setSpeed(float rpm) {
    pio_sm_set_enabled(pioInstance, stateMachine, false);
    speed = rpm;
    float div = calculateClkDiv(rpm);
    pio_sm_set_clkdiv(pioInstance, stateMachine, div);
    pio_sm_set_enabled(pioInstance, stateMachine, true);
}

void StepperMotor::resetStepCounter(void) { stepCounter = 0; }

void StepperMotor::stop() {
    pio_sm_set_enabled(pioInstance, stateMachine, false);

    sequenceCounter = modulo(getCurrentStep() + 1, 8);
    if (direction == ANTICLOCKWISE) { sequenceCounter = modulo(7 - (sequenceCounter - 1) + 1, 8); }
    uint fifoLevel = pio_sm_get_tx_fifo_level(pioInstance, stateMachine);
    int32_t stepsLeft = read_steps_left();
    stepCounter = modulo(stepCounter - stepsLeft, stepMax);

    for (uint i = 0; i < fifoLevel; i++) {
        stepCounter = modulo(stepCounter - (int16_t)(stepMemory & 0xffff), stepMax);
        stepMemory >>= 16;
    }

    pio_sm_clear_fifos(pioInstance, stateMachine);
    pio_sm_exec(pioInstance, stateMachine, pio_encode_jmp(0));
    pio_sm_set_enabled(pioInstance, stateMachine, true);
}

void StepperMotor::off() {
    // TODO: make this work
    uint instr = pio_encode_set(pio_pins, 0) | pio_encode_sideset(2, 0);
    pio_sm_exec(pioInstance, stateMachine, instr);
    return;
}
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

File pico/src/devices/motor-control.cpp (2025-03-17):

#include "motor-control.hpp"

#define NATURAL_SPEED 3

// these are used for calibration
static MotorControl *motorcontrol;

MotorControl::MotorControl(std::shared_ptr<StepperMotor> horizontal, std::shared_ptr<StepperMotor> vertical,
                           int optopin_horizontal, int optopin_vertical)
    : motor_horizontal(horizontal), motor_vertical(vertical), opto_horizontal(optopin_horizontal),
      opto_vertical(optopin_vertical), horizontal_calibrated(false), vertical_calibrated(false),
      horizontal_calibrating(false), vertical_calibrating(false), handler_attached(false), heading_correction(M_PI_2) {
    init_optoforks();
    motorcontrol = this;
    motor_horizontal->init(pio0, 5, CLOCKWISE);
    motor_vertical->init(pio1, 5, CLOCKWISE);
}

void MotorControl::setHeading(double heading) {
    // -90 degrees (half pi) because of physical orientation of camera
    heading_correction = normalize_radians(M_PI_2 + (heading * M_PI / 180.0));
}

bool MotorControl::turn_to_coordinates(azimuthal_coordinates coords) {
    if (coords.altitude < MIN_ANGLE || coords.altitude > MAX_ANGLE) {
        DEBUG("Altitude below horizon, can't turn the motor");
        return false;
    }
    coords.azimuth = normalize_radians(coords.azimuth + heading_correction);

    if (coords.azimuth > MAX_ANGLE) {
        coords.azimuth -= MAX_ANGLE;
        if (coords.altitude < (M_PI / 2))
            coords.altitude += M_PI - 2 * coords.altitude;
        else
            coords.altitude -= M_PI + 2 * coords.altitude;
    }
    DEBUG("Motor azimuth:", coords.azimuth * 180 / M_PI, "altitude:", coords.altitude * 180 / M_PI);
    double ratio = fabs(motor_horizontal->get_position() - coords.azimuth) /
                   fabs(motor_vertical->get_position() - coords.altitude);
    double horizontal_speed = NATURAL_SPEED * ratio;
    motor_vertical->setSpeed(NATURAL_SPEED);
    motor_horizontal->setSpeed(horizontal_speed);
    motor_horizontal->turn_to(coords.azimuth);
    motor_vertical->turn_to(coords.altitude);
    return true;
}

void MotorControl::off(void) {
    horizontal_calibrated = false;
    vertical_calibrated = false;
    motor_horizontal->off();
    motor_vertical->off();
}

//// PRIVATE ////

void MotorControl::init_optoforks(void) {
    if (opto_horizontal) {
        gpio_set_dir(opto_horizontal, GPIO_IN);
        gpio_set_function(opto_horizontal, GPIO_FUNC_SIO);
        gpio_pull_up(opto_horizontal);
    }
    if (opto_vertical) {
        gpio_set_dir(opto_vertical, GPIO_IN);
        gpio_set_function(opto_vertical, GPIO_FUNC_SIO);
        gpio_pull_up(opto_vertical);
    }
}

bool MotorControl::isCalibrated(void) const { return horizontal_calibrated && vertical_calibrated; }

bool MotorControl::isCalibrating(void) const { return horizontal_calibrating || vertical_calibrating; }

bool MotorControl::isRunning(void) const { return motor_horizontal->isRunning() || motor_vertical->isRunning(); }

//// CALIBRATION ////

void raw_calibration_handler(void) {
    if (!motorcontrol) {
        DEBUG("Motor control raw calibration called without initializing");
        return;
    }
    int horizontal_opto = motorcontrol->opto_horizontal;
    int vertical_opto = motorcontrol->opto_vertical;
    if (horizontal_opto) {
        if (gpio_get_irq_event_mask(horizontal_opto) & GPIO_IRQ_EDGE_RISE) {
            gpio_acknowledge_irq(horizontal_opto, GPIO_IRQ_EDGE_RISE);
            motorcontrol->calibration_handler(HORIZONTAL, true);
        } else if (gpio_get_irq_event_mask(horizontal_opto) & GPIO_IRQ_EDGE_FALL) {
            gpio_acknowledge_irq(horizontal_opto, GPIO_IRQ_EDGE_FALL);
            motorcontrol->calibration_handler(HORIZONTAL, false);
        }
    }
    if (vertical_opto) {
        if (gpio_get_irq_event_mask(vertical_opto) & GPIO_IRQ_EDGE_RISE) {
            gpio_acknowledge_irq(vertical_opto, GPIO_IRQ_EDGE_RISE);
            motorcontrol->calibration_handler(VERTICAL, true);
        } else if (gpio_get_irq_event_mask(vertical_opto) & GPIO_IRQ_EDGE_FALL) {
            gpio_acknowledge_irq(vertical_opto, GPIO_IRQ_EDGE_FALL);
            motorcontrol->calibration_handler(VERTICAL, false);
        }
    }
}

void MotorControl::calibrate(void) {
    if (isCalibrating()) return;
    if (!opto_horizontal) return;
    if (!opto_vertical) return;
    motor_horizontal->stop();
    motor_vertical->stop();
    DEBUG("Calibration started.");

    motor_horizontal->setSpeed(15);
    motor_vertical->setSpeed(15);
    motor_horizontal->setDirection(CLOCKWISE);
    motor_vertical->setDirection(CLOCKWISE);
    motor_horizontal->turnSteps(300);
    motor_vertical->turnSteps(300);
    while (isRunning())
        ;

    motor_horizontal->setSpeed(2);
    motor_vertical->setSpeed(2);
    motor_horizontal->setDirection(ANTICLOCKWISE);
    motor_vertical->setDirection(ANTICLOCKWISE);
    horizontal_calibrated = false;
    vertical_calibrated = false;
    horizontal_calibrating = true;
    vertical_calibrating = true;
    if (!handler_attached) {
        gpio_add_raw_irq_handler_with_order_priority(opto_horizontal, raw_calibration_handler,
                                                     PICO_HIGHEST_IRQ_PRIORITY);
        gpio_add_raw_irq_handler_with_order_priority(opto_vertical, raw_calibration_handler, PICO_HIGHEST_IRQ_PRIORITY);
        handler_attached = true;
    }
    gpio_set_irq_enabled(opto_horizontal, GPIO_IRQ_EDGE_RISE | GPIO_IRQ_EDGE_FALL, true);
    gpio_set_irq_enabled(opto_vertical, GPIO_IRQ_EDGE_RISE | GPIO_IRQ_EDGE_FALL, true);
    if (!irq_is_enabled(IO_IRQ_BANK0)) irq_set_enabled(IO_IRQ_BANK0, true);

    motor_horizontal->turnSteps(6000);
    motor_vertical->turnSteps(6000);
}

void MotorControl::calibration_handler(Axis axis, bool rise) {
    if (axis == HORIZONTAL) {
        if (!rise) {
            if (!isCalibrated()) {
                motor_horizontal->stop();
                motor_horizontal->resetStepCounter();
                motor_horizontal->setDirection(CLOCKWISE);
                horizontal_calibrated = true;
                horizontal_calibrating = false;
            }
        }
    }
    if (axis == VERTICAL) {
        if (!rise) {
            if (!isCalibrated()) {
                motor_vertical->stop();
                motor_vertical->resetStepCounter();
                motor_vertical->setDirection(CLOCKWISE);
                // motor_vertical->turnSteps(100);
                vertical_calibrated = true;
                vertical_calibrating = false;
            }
        }
    }
}

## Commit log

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2024-11-22 quickfix to pico docker to make sure it has access to common dir
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2024-11-25 Add 3D-models to project.
    [28BYJ-48-cover.SLDPRT, 28BYJ-48-stepper-motor.sldprt, Connector-arm.SLDPRT]
2024-11-25 set_nmea_output command doesn't seem to work
    [gps.cpp, main.cpp]
2024-11-26 gps testing, minor fixes
    [gps.cpp, main.cpp]
2024-12-03 Redesigned models to better fit printer capabilities.
    [28BYJ-48-cover.SLDPRT, Connector-arm.SLDPRT, ESP-Holder.SLDPRT]
2024-12-08 compass returns its current heading when called with getHeading function
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2024-12-09 Added docker compose and Dockerfile to build and flash esp32 on linux machines
2024-12-10 Added all exported filetypes
    [28BYJ-48-cover.3MF, 28BYJ-48-cover.AMF, 28BYJ-48-cover.STL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]
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2024-12-12 modified stepper motor design based on feedback
    [28BYJ-48-cover.3MF, 28BYJ-48-cover.AMF, 28BYJ-48-cover.SLDPRT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]
2024-12-14 Added pico source files for planet finding. Also added unity unit test files for unit testing on pico
2024-12-16 clock: removed unnecessary sleeps and prints, revert main comments
    [main.cpp]
2024-12-16 Refactor Camera class to improve image handling and initialization logic
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2024-12-16 Enhance SDcard class mount configuration with additional parameters
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2024-12-16 webserver: print settings, fix upload api
2024-12-16 Basic stepper motor control library, right now only has functions to moveit by steps
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2024-12-19 pico: add helper method for converting updating time with str
2024-12-19 Add timer callback for sending GET requests and refactor task initialization
2024-12-19 Rename EspPicoCommHandler to EspPicoUartCommHandler and implement UART data send/receive methods
2024-12-19 pico: comms move stuff to individual files, still WIP
2024-12-19 Using doubles instead of floats, also fixed local sidereal time calculation
    [moon_finder.py, planet_finder.cpp]
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2024-12-20 added tests for orbital elements. added some prototypes for classes. added coordinate changes
2024-12-23 webserver: minor tweak, user page now has current name filled in by def
2024-12-23 pico: comms adjust sleep, clean, dprint enable for test
2024-12-28 more coordinate calculation, not working
    [planet_finder.cpp]
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2025-01-02 Refactor WirelessHandler constructor to accept SSID and password parameters
2025-01-02 Update SDcard class to reduce default max_open_files and add debug message for successful mount
2025-01-02 Refactor Camera class constructor and improve error handling in take_picture_and_save_to_sdcard method
    [camera.cpp]
2025-01-02 Add debug functions to print free PSRAM and largest free block
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2025-01-04 Refactor Camera constructor to improve parameter handling and remove unused variables
2025-01-04 Enhance SDcard class with mount point accessors and improved error handling during SD card mounting
    [sd-card.cpp]
2025-01-04 Increase stack size for init_task to improve task execution stability
    [main.cpp]
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2025-01-14 refactor: update UART configuration and enhance response handling in EspPicoCommHandler
2025-01-14 refactor: enhance SD card mounting logic with retry mechanism
2025-01-14 refactor: reorganize task handling and enhance UART data processing
2025-01-14 refactor: streamline app_main function and implement UART communication test
2025-01-14 feat: add get_datetime function to retrieve current timestamp
2025-01-14 bugfix: fix infinite read period on Uart read.
    [main.cpp, tasks.cpp]
2025-01-14 Compass accuracy is improved by taking into account the declination angle. Also fixed a minor bug.
    [compass.cpp]
2025-01-16 Added calibration for the compass, after testing seems to have made the compass more accurate.
2025-01-16 Restructured initialization. Now works with all (almost) pin configurations
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2025-01-19 pico: minor gps fix; gpg toggles weren't being used, sstate to private
    [gps.cpp]
2025-01-20 refactor: replace CameraReturnCode with int for method return types and enhance documentation
    [camera.cpp, camera.hpp]
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2025-01-21 a small fix for compass calibration... compass was tested multiple times and acquired satisfactory results. Also acquired some interesting information about the compass.
    [compass.cpp]
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2025-01-21 Made modifications to 3D parts based on prior testing.
    [28BYJ-48-cover.3MF, 28BYJ-48-cover.AMF, 28BYJ-48-cover.SLDPRT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]
2025-01-22 feat: implement request handling and timer management in tasks.cpp
2025-01-22 feat: add debug logging for camera initialization process
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2025-01-26 docs: update Readme.md with custom partition table instructions and add partitions.csv file
    [partitions.csv]
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2025-01-27 little fix to stepper motor, and start of getting timestamps
    [planet_finder.cpp, stepper-motor.cpp]
2025-01-28 feat: update UART baud rate to 115200 and comment out debug log disabling
2025-01-28 Various bug and typo fixes.
    [espPicoUartCommHandler.cpp, main.cpp, tasks.cpp]
2025-01-28 Add newest designs.
    [Connector-arm.3MF, Connector-arm.AMF, Connector-arm.SLDPRT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]
2025-01-28 minor fix to optofork holder design.
    [Opto-fork-holder.3MF, Opto-fork-holder.AMF, Opto-fork-holder.SLDPRT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]
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2025-02-01 bugfix: fix typo in wirelessHandler init.
    [tasks.cpp]
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2025-02-04 feat: improve task initialization and error handling with enhanced debug logging
    [tasks.cpp]
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2025-02-06 feat: add functions to find character position and extract messages from UART buffer
2025-02-06 feat: enhance UART data handling with improved message extraction and error checking
    [tasks.cpp]
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2025-02-07 Add model for optofork, baseplate, and add minor updates to old models.
    [28BYJ-48-bottom-plate.SLDPRT, 28BYJ-48-bottom-plate.STL, 28BYJ-48-cover.SLDPRT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]
2025-02-07 Minor modifications to arm model
    [Connector-arm.SLDPRT, Connector-arm.STL, Gyro-arm-assembly.SLDASM]
2025-02-07 refactor: optimize debug print function for better handling of integral and floating-point types
2025-02-07 refactor: enhance camera initialization with detailed error handling and retry logic
    [camera.cpp]
2025-02-07 fix: correct loop condition in find_first_char_position function
    [espPicoUartCommHandler.cpp]
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2025-02-09 feat: update image ID handling and add diagnostics request processing in UART tasks
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2025-02-11 Updated models.
    [28BYJ-48-bottom-plate.SLDPRT, 28BYJ-48-bottom-plate.STL, Connector-arm.SLDPRT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]
2025-02-14 feat: enhance error handling and update time synced status in web server request task
    [tasks.cpp]
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2025-02-17 refactor: Replace manual mutex management with ScopedMutex in SDcardHandler
    [sd-card.cpp]
2025-02-17 got the low power mode to somewhat work. need to add something to address the interrupts triggered outside the wake up interrupt.
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2025-02-17 Add new bottom bowl 3D model
    [28BYJ-48-bottom-plate.SLDPRT, Bottom-bowl.SLDPRT, Bottom-bowl.STL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]
2025-02-17 Add bottom bowl design.
    [28BYJ-48-bottom-plate.STL, Connector-arm.STL, ESP-Holder.STL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]
2025-02-17 Remove unused filetypes
    [28BYJ-48-bottom-plate.STL, 28BYJ-48-cover.3MF, 28BYJ-48-cover.AMF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]
2025-02-17 turn to coordinate. also sets speed so the motors try to finish at the same time
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2025-02-18 webserver: diagnostics page switch fix, styling
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2025-02-19 pico: sleep functions fix
2025-02-20 refactor: Replace manual buffer allocation with ScopedBuffer in SDcardHandler
    [sd-card.cpp]
2025-02-21 fix: Ensure proper unmounting of SD card and reset file mutex in SDcardHandler destructor
    [sd-card.cpp]
2025-02-21 feat: Add unit tests for SD card and JSON parser functionality
    [partitions.csv]
2025-02-21 refactor: Replace std::map with std::unordered_map for improved performance
    [sd-card.cpp]
2025-02-21 refactor: Replace std::map with std::unordered_map for settings storage and enhance Wi-Fi/server settings handling
    [tasks.cpp]
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2025-02-23 refactor: remove TODO comments and improve error handling in task functions
    [tasks.cpp]
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2025-02-24 pico: fixes for roni
    [controller.cpp]
2025-02-25 pico: fix master build
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2025-02-27 Added screw holes for bowl and plate, enlarged wire hole, fixed ESP holder wall height
    [28BYJ-48-bottom-plate.SLDPRT, 28BYJ-48-bottom-plate.STL, Bottom-bowl.SLDPRT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]
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2025-03-01 refactor: add SOCKET_RECEIVE_FAIL return code and improve error handling in sendRequest method
2025-03-01 refactor: enable TLS support and enhance UART data handling with improved debug messages
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2025-03-02 refactor: fix loop condition in find_first_char_position for correct buffer length
    [espPicoUartCommHandler.cpp]
2025-03-04 config: reduce stack size for send_request_to_websrv_task and update message type to DEVICE_STATUS
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2025-03-06 pico: more main loop stuff, fix warning date_utils
    [commbridge.cpp, controller.cpp, gps.cpp]
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2025-03-07 config: enhance device status handling and add error logging for picture capture
    [tasks.cpp]
2025-03-07 Fix: fix pin definitions, I2C defiiniton for compass, and added debug prints
    [main.cpp]
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2025-03-07 error checking in compass function
    [compass.cpp]
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2025-03-08 added corrections to heading
    [controller.cpp, motor-control.cpp]
2025-03-08 fix: take multiple images to fix green filter problem.
    [camera.cpp]
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2025-03-08 fix return of get all commands
    [storage.cpp]
2025-03-08 Changed Esp holder design to hopefully get better grip
    [ESP-Holder - BACKUP.SLDPRT, ESP-Holder.SLDPRT, ESP-Holder.STL]
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2025-03-09 Add 3rd esp holder design with nut locks.
    [ESP-Holder-Nut-Lock-Design.SLDPRT, ESP-Holder-Nut-Lock-Design.STL]
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2025-03-11 sd-card: improve error handling for settings reading
    [sd-card.cpp, tasks.cpp]
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2025-03-11 fix assembly file name
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2025-03-12 refactor: improve documentation and error handling in CameraHandler class
    [camera.cpp]
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2025-03-12 docs: add detailed documentation for error handling in data processing functions
    [sd-card.cpp]
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2025-03-13 pico: code documentation, cleanup, minor fixes
    [PicoUart.cpp, commbridge.cpp]
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2025-03-19 Fix typo: 3D-Models/CMakeLists.txt -> esp32-cam/CMakeLists.txt
2025-03-19 Fix typo: Forgot to fix all instances of the typo in commit: 7b4098ee 3D-models/CMakeLists.txt -> esp32-cam/CMakeLists.txt
